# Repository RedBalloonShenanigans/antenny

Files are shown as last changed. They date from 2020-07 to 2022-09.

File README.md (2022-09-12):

# Antenny

Make your own base station to communicate with satellites!

We have a [discord server](https://discord.com/invite/nsSMEdv) for collaboration, questions, and show and tell off!

## Setting up the hardware

### Important Notice:
- Pin conflict: Do NOT use the folloing pins for GPIO if you are using SPIRAM firmware:
```
# known_confilit_pins = [
#     0, 1, 3, 6, 7, 
#     8, 9, 10, 11, 12, 
#     13, 16, 17, 20, 24, 
#     28, 29, 30, 31
# ]
```
- Pin that is input only
```
# input_only_pins = [34, 35, 36, 37, 38, 39]
```

### Jumpers

#### Required Antenny Jumpers
- On the antenny MK7 there are two required jumpers, labeled `JUMPER FOR PWN DR` on the back of the board. This will 
bridge the GPIO to the on board PWM Driver. 

#### Optional Antenny Jumpers

- The antenny MK7 provides jumpers to breakout pins 4, 26, 27, VCC and GND to the header labeled `P11` for the IMU. 
To use this header, you must solder the jumpers labeled `JUMPER FOR IMU`, otherwise, just used the ESP32 GPIO headers.

- To use wifi, either provide a antenna to the ESP32s on board jack, or solder the jumper next to the antenna 
connector labeled `R15` on the ESP32. See below picture. 

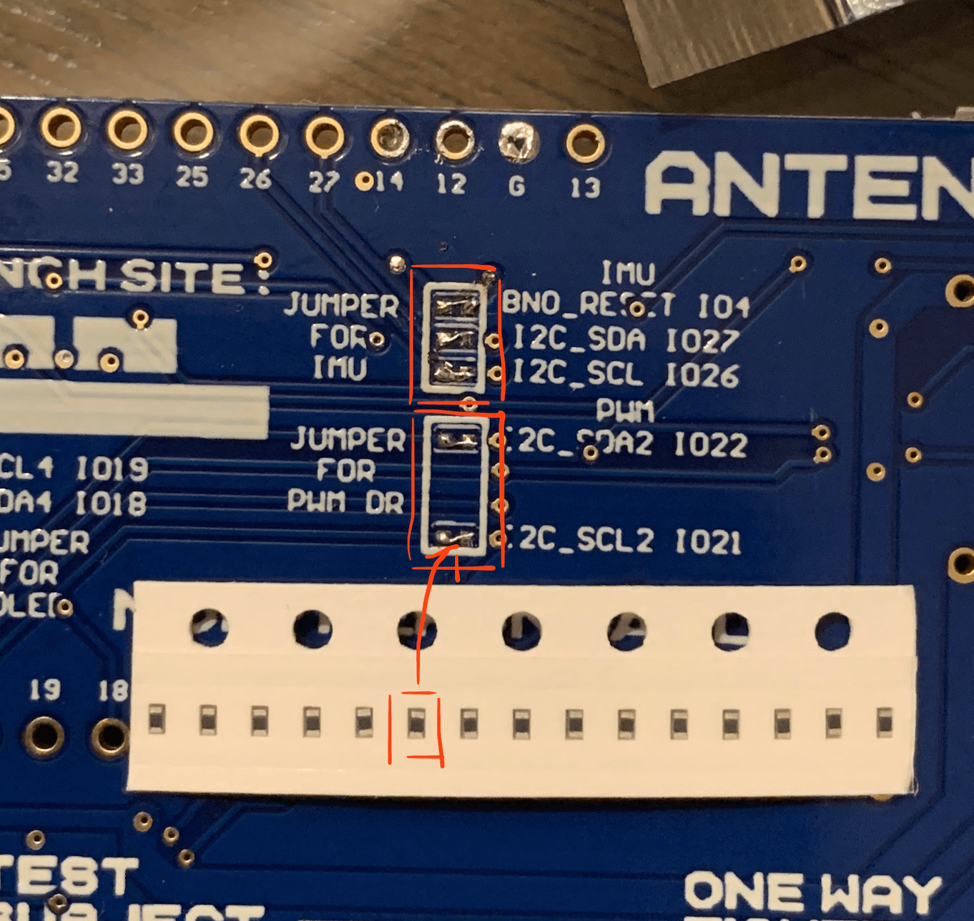
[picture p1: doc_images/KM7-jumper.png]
Antenny KM7 jumper

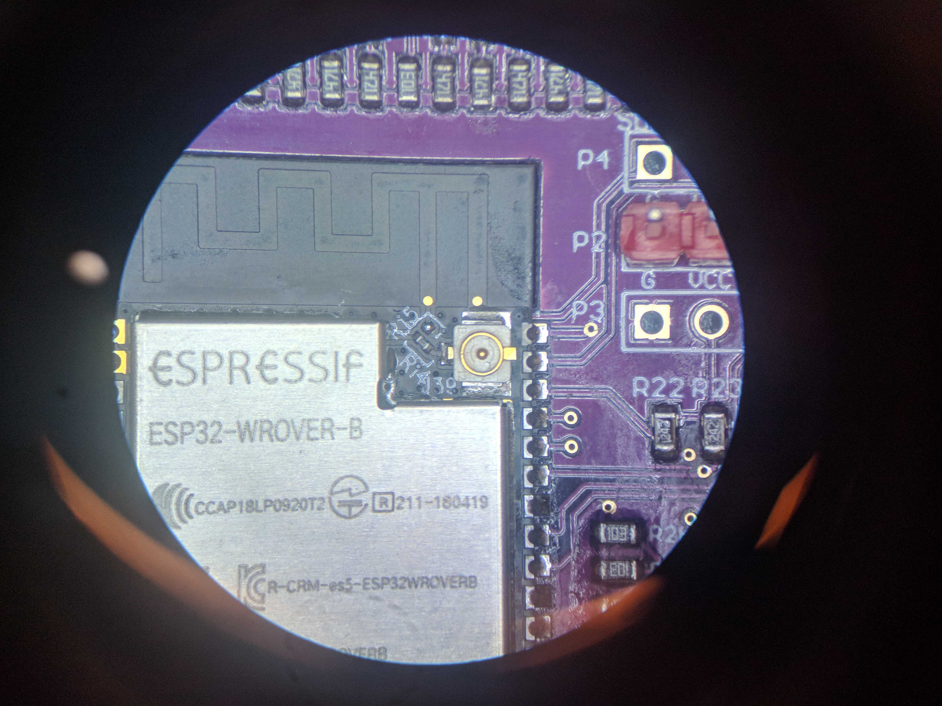
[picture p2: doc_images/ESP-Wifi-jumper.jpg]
Antenny KM7 jumper


- Important: When you start to program the Antenny board with esptool, please hold the K2 Tact Button until the program detect the download mode.

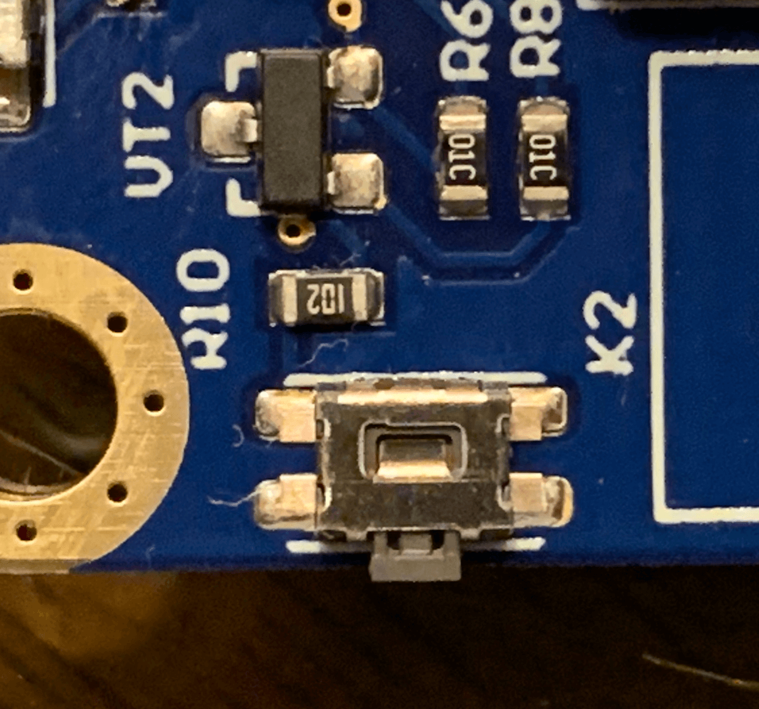
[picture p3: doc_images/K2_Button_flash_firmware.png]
Flash Firmware button


#### Optional IMU Jumper
There is one optional IMU jumper. This is used to select the IMU mode. More info can be found in the [BNO080 
datasheet](https://cdn.sparkfun.com/assets/1/3/4/5/9/BNO080_Datasheet_v1.3.pdf)
If you do not want to use the jumper, you can use pins to select the correct mode. This can also be useful for 
switching between modes in software. 

The mode we use is the Robotic Vacuum Cleaner (RVC) mode. To enable this you can provide power to the PS0 pin using 
the jumper as shown below. 

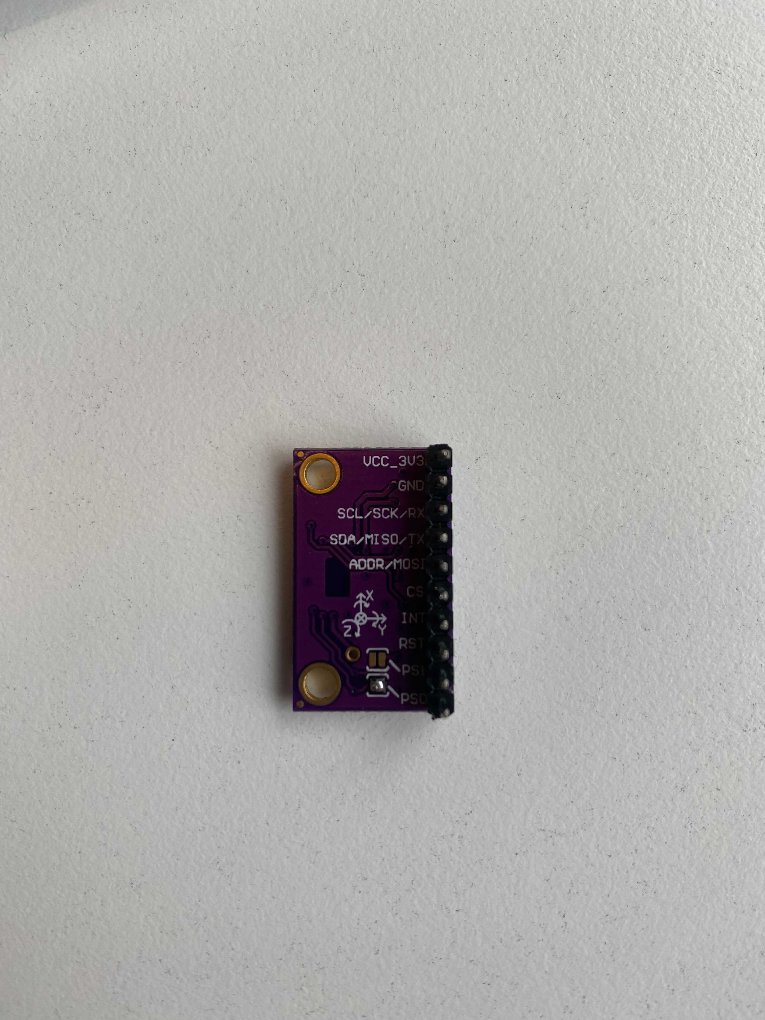
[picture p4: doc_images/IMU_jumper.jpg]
BNO080 Jumper


### Setting up the platform
This will go over how to setup the servo gimbal, IMU and antenny board. I used hot glue to secure the hardware, but 
more creative approaches are welcome. 

####Step 1: Position the IMU
Position the IMU on the gimbal arm. The position show below will give the correct orientation. If you want a 
different IMU position, you can correct the elevation angle in software. 

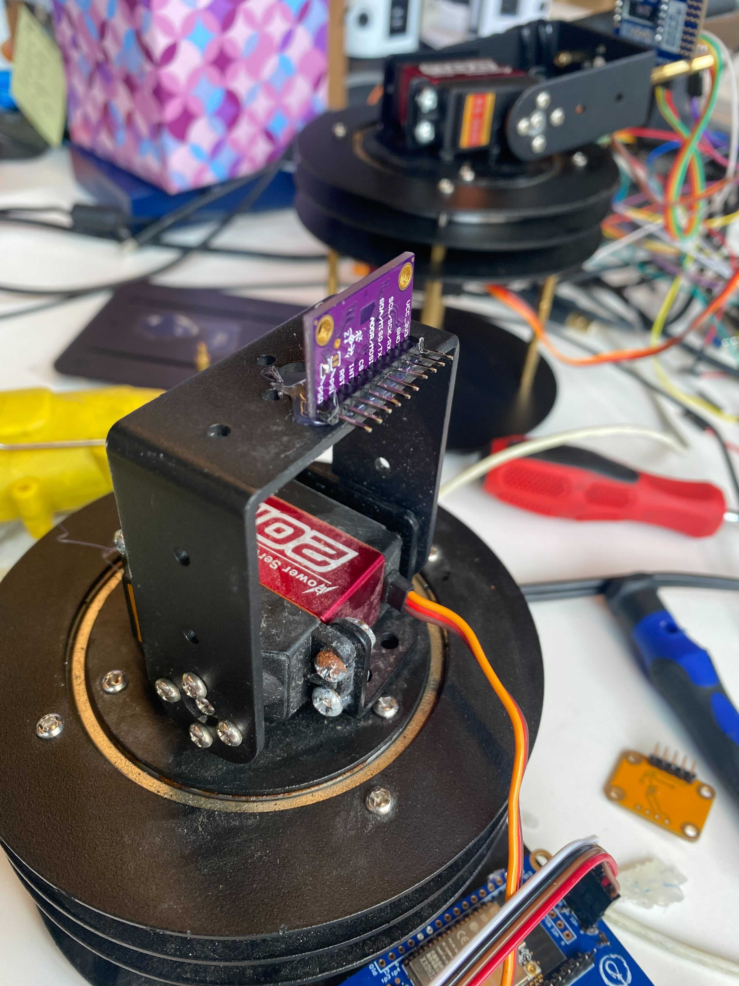
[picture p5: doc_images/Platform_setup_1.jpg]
Platform Step 1


#### Step 2: Position the Antenny
Next we secure the Antenny to the platform. It is advised to isolate the pins from any metal contact.

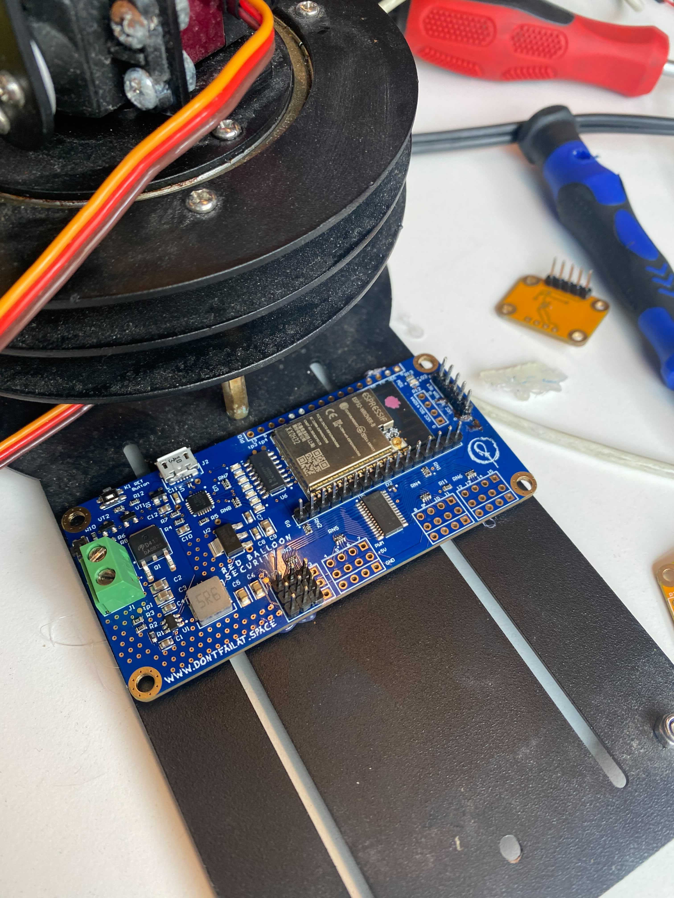
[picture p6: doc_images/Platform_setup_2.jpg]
Platform Step 2


### Step 3: Wire the IMU Communication Lines
NOTE: From this point on, the pins you use are configurable from the `antenny_config`, as described in the software 
guide below. To verify your pins or reconfigure as you wish, it is suggested you edit the config through the 
`antenny_manual_setup` command described in the software guide. 

The IMU communication lines are labeled on both the IMU PCB and the Antenny PCB, just match them up, as shown. 

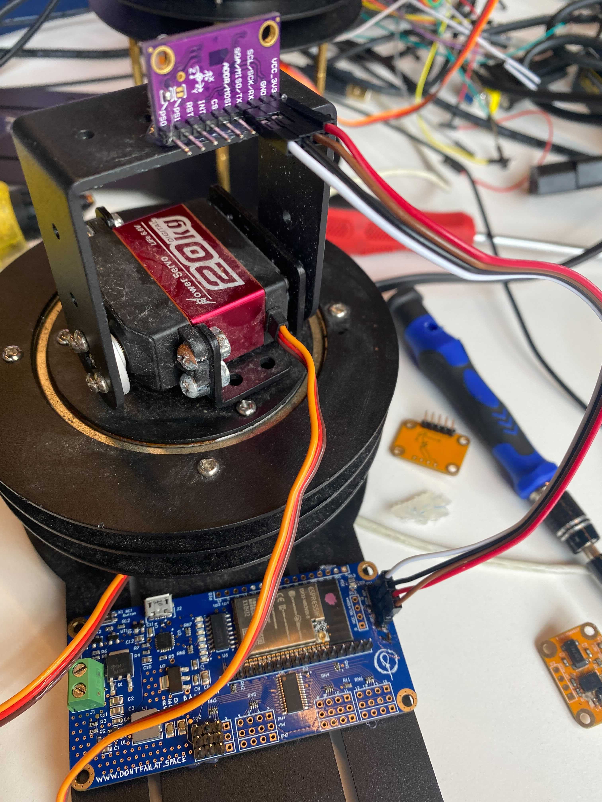
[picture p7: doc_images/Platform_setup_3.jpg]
Platform Step 3


### Step 4: Wire the IMU Reset Line
Same as step 3, it is labeled.

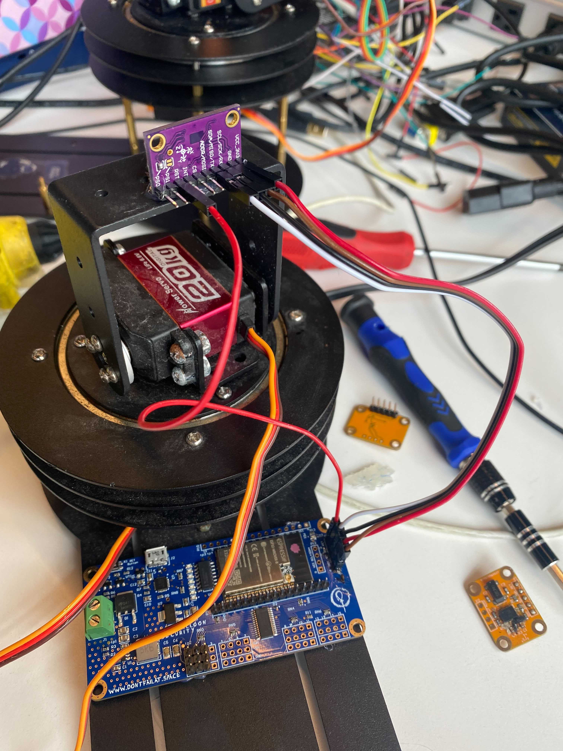
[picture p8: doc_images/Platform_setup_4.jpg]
Platform Step 4


### Step 5: Wiring the Program Select Pins (Optional):
If you did not solder the IMU jumper, you must pick two pins to use to control PS0 and PS1. If using this approach, 
its suggested you setup these pins using the `antenny_manual_setup`. 

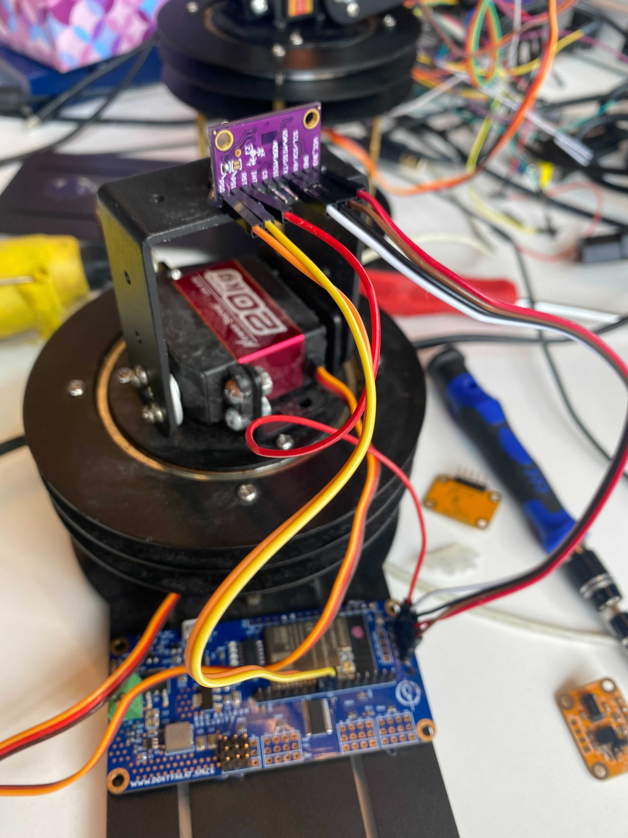
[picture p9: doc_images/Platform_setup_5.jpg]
Platform Step 5


### Step 6: Wiring the Servos
Next we wire the servos to the PWM controller. By default the elevation(top) servo goes to pwm index 0 and azimuth
(bottom) goes to index 1, but this is, again, configurable. 

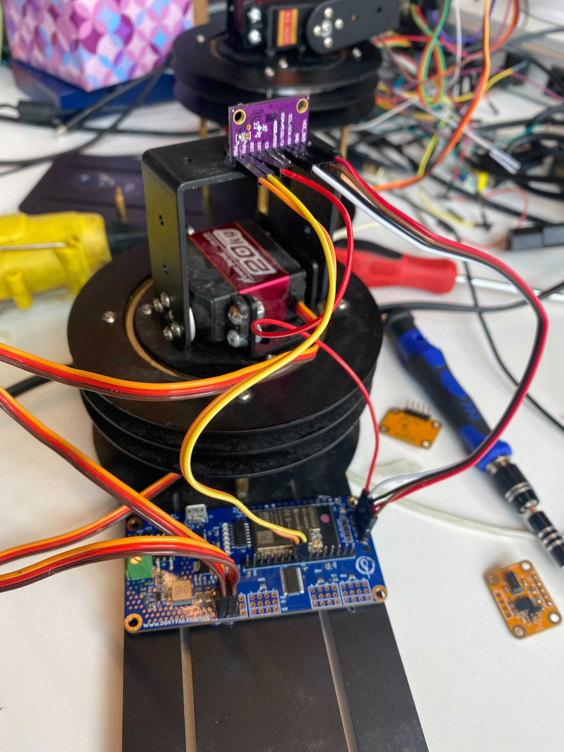
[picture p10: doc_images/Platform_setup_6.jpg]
Platform Step 6


# Installing the Antenny software

## Installing Micropython
1. Download and install the USB driver for the CP210 USB to UART chip [here](https://www.silabs.com/developers/usb-to-uart-bridge-vcp-drivers)

2. Download esptool from [here](https://github.com/espressif/esptool/)

3. Put the ESP into download mode (see above) and erase your ESP32

    Example: ```python3 -m esptool --port /dev/tty.SLAB_USBtoUART erase_flash```
    
4. Download the micropython firmware from [here](https://micropython.org/resources/firmware/esp32spiram-20210623-v1.16.bin)

5. Put the ESP into download mode (see above) and re-flash the Micropython firmware

    Example: ```python3 -m esptool --chip esp32 --port /dev/tty.SLAB_USBtoUART --baud 115200 
write_flash -z 0x1000 ~/Downloads/esp32spiram-20210623-v1.16.bin```

## Installing Antenny MP Code
0. We use MPFShell to upload the python files to the board. First you must install this on your host computer with 
`python3 -m pip install mpfshell`.
1. To begin install, first push the reset button on the antenny board, labeled `RET Button`.
2. Next, from the root directory of this repository, run  the `make nyansat` make directive with the `SERIAL` 
argument pointing to your antenny block device.

    Example: `make nyansat SERIAL=/dev/tty.SLAB_USBtoUART`
3. The Installer will give you a series of prompts.
    - `Do you want to do an installation of all components and libraries?(Y/n)`
    
        - If this is your first install, or you would like to do a fresh install of all code select `Y`, otherwise, 
        if you would only like to install specific components select `N`.
        
    - If you selected `Y` for the previous prompt you will see:
    
        - `Are you sure you want to erase all files on the device? (y/N)`
    
            - This is just a confirmation, as a full install will take a bit of time.
        
    - If you selected `N` you will see:
    
        - `Name a component you wish to install:`
        
            - If you are developing new components or making fixes to existing ones, you can upload one component at 
            a time by typing its name into this prompt. That name should correspond to a sub directory found in the 
            [station](https://github.com/RedBalloonShenanigans/antenny/tree/master/nyansat/station) directory. For 
            example selecting `imu` would upload all code in the [imu](https://github.com/RedBalloonShenanigans/antenny/tree/master/nyansat/station/imu) sub directory.
            
        - `Do you wish to install more? (y/N)`
        
            - Use this to repeat the above step.
            
        - `Do you want to keep the configs on the device? (Y/n)`. 
        
            - If you would like to restart your antenny configs from the repository state, select `N`, to keep your 
            configs on board select `Y`. 
            
        - `Do you want to re-install the libraries (y/N)`
        
            - Select yes to reinstall the libraries found [here](https://github.com/RedBalloonShenanigans/antenny/tree/master/lib)
            
4. You should see the installer upload the code to the antenny. 

5. You will see the installer report `False` upon completion, press `Enter` to continue.

6. The installer will prompt you for your WiFi info. If the above steps were taken to enable WiFi, enter your info, 
otherwise leave blank.

Your installation is complete!     

# Getting Started

## Entering the Python interpreter

1. Using a terminal utility of your choice, enter the devices python interpreter.

    - Examples:

        `screen <block device> 115200`
        
        or
        
        `minicom -D <block device> -b 115200`
        
    - In the case of windows, Putty is suggested.

2. Upon entering the interpreter you should be met with the python prompt `>>>`. If you are not try the reset button 
on the side of the board or revisit the `Installing Micropython` section of this README.

3. To view any potential import errors, press the reset button on the board as described in the installation section. 

     - In micropython, the first script run on startup will always be `boot.py` followed by `main.py`. 
     The `main.py` script will import all relevant antenny code and provide access to `api`, an instance of 
[AntennyAPI](https://github.com/RedBalloonShenanigans/antenny/blob/master/nyansat/station/api/api.py). 

## Using the Antenny API

### Device Startup

Once your hardware is properly setup and you have installed the antenny station code, you can begin working with the 
device. To interface with the device from the python interpreter, we will use member methods of the `api` class. 

#### High Level Methods

High level methods start with `antenny_` are used to setup your antenny assembly, calibrate and save calibration data. 

- `api.antenny_init_components()`

    - Initializes the components described by the current config. For more info on device configuration, please see 
    the "Configuring Antenny" section. 
    
- `api.antenny_calibrate()`

    - Calibrates the antenny platform. 
    - NOTE: This will start the automatic calibration routine. Currently, IMU calibration only supported by the BNO055 
    IMU. BNO080 support expected soon.
    
- `api.antenny_save(name: Optional)`

    - Saves the current configuration of each component as default. With an optional name. Makes the state of the 
    configuration and calibration persistent. 
    
- `api.antenny_manual_setup()`

    - This will walk you through manual configuration of the antenny board and its components. Useful if it is your 
    first time setting up, or for easier access to some of the more useful config entries.

#### Platform Methods

Platform methods start with `platform_` and are used to operate the platform, a term used in this project to describe 
the pwm driver, the motors it is driving, the IMU and the antenny board as a single assembly. 

- `api.platform_orient()`
 
    - Orients the platform to its current position. Should be run after repositioning the gimbal platform. This finds
     the 90 degree dead zone of the azimuth servo.
     
- `api.platform_start()`

    - Enables movement of the platform. Commands can be issued to point at specific coordinates.
    
- `api.platform_stop()`

    - Disables movement of the platform. Commands can be issues to manually move the servods or re-orient the platform.
    
- `api.platform_set_azimuth(az: int)`

    - Sets the azimuth coordinate of the platform while movement is enabled. 
    
- `api.platform_set_elevation(el: int)`

    - Sets the azimuth coordinate of the platform while movement is enabled. 

- `api.platform_set_coordinates(az: int, el: int)`

    - Sets both coordinates of the platform while movement is enabled.
    
#### Servo Methods

Each individual servo can be operated manually through these methods. Without access to the IMU the servos will not 
know they're orientation.

- `api.elevation_servo_set_position`
- `api.azimuth_servo_set_position`

    - Sets the position of the elevation servo. The current specs for the servos provided with the antenny put the 
    position argument in range(0, 4096), however only a subset of that range will actually move the servo.
    
- `api.elevation_servo_set_min_max(min: int, max: int)`
- `api.azimuth_servo_set_min_max(min: int, max: int)`

    - Sets the minimum and maximum `position` arguments that allow the servo to move, part of the higher level 
    calibration step. 

#### IMU Methods

IMU data can be accessed directly from the API as well. 

- `api.imu_get_azimuth()`

    - Returns the azimuth in degrees as reported by the IMU
    
- `api.imu_get_elevation()`

    - Returns the elevation in degrees as reported by the IMU
    
- `api.imu_get_euler()`

    - Returns the euler angles in order of yaw, roll, pitch. 
    
The IMU can also be manually calibrated

- `api.imu_calibrate()`

    - Begins the calibration routine. For best results, follow the printed instructions from the console. 
    
#### Other

There are plenty of other methods, most used for debugging, available to the user, as well as direct access to 
underlying components. For more information, reading through the antenny code is advised.      

### Configuring Antenny
NOTE: These configs have wrappers to properly alter the config members before saving in the API. In general only the 
High Level `api.antenny_save(name: Optional)` should be used by users. 

Your hardware is described by a series of 
[configs](https://github.com/RedBalloonShenanigans/antenny/tree/master/nyansat/station/configs) that can be updated 
through your installer or on the antenny board itself. This section will go over on baord config modification. To use 
the installer re-visit the above guide.

The api uses the 
[Config](https://github.com/RedBalloonShenanigans/antenny/blob/master/nyansat/station/config/config.py) class to 
manage configs and are exposed by the `AntennyAPI`. There are currently three configs used by the antenny system, but
 any components that require information to be stored across boots should use its own config.
 
#### Antenny API Config classes
    
- `api.antenny_config`
    - The [antenny_config](https://github.com/RedBalloonShenanigans/antenny/tree/master/nyansat/station/configs/antenny) 
describes the base station integration with pin connections as well as high-level attributes like current longitude and latitude.
    - Help information for each antenny_config member can be retrieved via `api.antenny_config_help()`

- `api.imu_config`
    - The [imu_config](https://github.com/RedBalloonShenanigans/antenny/tree/master/nyansat/station/configs/imu) 
    describes calibration data of the IMU. Currently only available for the BNO055, for more details on this you can 
    view the BNO055 and BNO08x data sheets.

- `api.servo_config`
    - The [servo_config](https://github.com/RedBalloonShenanigans/antenny/tree/master/nyansat/station/configs/servo) 
    describes the limits of the servo motors.

#### Config Methods

- `Config.set(<member>, <value>)`: Sets a config to a new value.

- `Config.get(<member>)`: Gets the current value of a config member.

- `Config.save(name: Optional)`: Saves the current config to the device, with a new name option for multiple configs.

- `Config.load(name: Optional)`: Loads the currently saved values, if name is specified, loads from a previously 
saved config, if it is not, reloads the last save of the current config.

- `Config.save_as_default_config()`: The current config will be loaded on reboot. 

- `Config.load_default_config()`: Load the config that was present on reboot.

## The Antenny Host System
Under Development...

Cooperation between the antenny board and another system is possible through the antenny client as well as the UDP 
Sender. Use of the client is not suggested while developing on or debugging the system, but could be useful for more 
interesting applications such as beacon tracking. 

### The Command Invoker
The `command_invoker` is a 1:1 library to the antenny `api` class found at `nyansat/host/shell/command_invoker.py`. The 
`command_invoker` calls out to the board through MPFShell to exec API commands. Feedback and error handling does not 
work very well so work should be offloaded to the board when possible. 

### Antenny Client
The `antenny_client`, found at `nyansat/host/shell/antenny_client.py` should use the command invoker to implement 
higher level functions in conjunction with more computationally expensive libraries. 

### Shell
Current depricated. 

The antenny client can then be integrated into the MPFShell environment through `nyansat/host/shell/__main__.py`. 
Commands of the format `do_<cmd>()` will be used as shell commands. See the file for examples. This shell can then be
 run through the command `make nyanshell`.

## Known Issues
- The BNO08x calibration never finishes :(
- The BNO08x euler angles are incorrect (maybe calibration, maybe I'm bad at math, probably both.)

##Requirements

- Python >= 3.6

NyanShell:

- MPFShell
- TUI-DOM

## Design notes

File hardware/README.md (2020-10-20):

# RBS Antenny Board 

If you want make your life a little simpler, we have a custom PCB for you! The Antenny board was designed and assembled by Red Balloon Security and you the ability to plug and play the NyanSat basic station with one single board and no complex wiring. Antenny combines the EPS32 (with Bluetooth and WIFI support), a 16 channel PWM driver, and a motor driver with a maximum output of maximum 27W at 6V. The RBS Antenny board can easily handle the movement control of NyanSat antenna gimbal, and you can load your own custom code to adjust it however you like. The onboard reserved I2C channel connectors allow you to extend the basic NyanSat setup with an RBS custom made IMU module, OLED screen and GPS module. After DEF CON, you can even repurpose the board for your future projects requiring microcontrollers and motor drivers.

The RBS Antenny board is designed using Altium Designer and Assembled by in-house pick and place machine in Manhattan, New York. Hardware design will be open sourced through our [GitHub repo](https://github.com/RedBalloonShenanigans/antenny/tree/master/hardware), and you can buy them in our store [link[. Feel free to check it out or make your own!  

## required items that are NOT included in package

- [Jumper Wires](https://www.amazon.com/EDGELEC-Breadboard-Optional-Assorted-Multicolored/dp/B07GD2BWPY/)
- [pin headers](https://www.amazon.com/MCIGICM-Header-2-45mm-Arduino-Connector/dp/B07PKKY8BX/)
- Soldering Iron Kit
- Power supply (6v-30v) or lipo battery

## Antenny board hardware setup guide and schematic

- [Setup guide and import updates](https://github.com/RedBalloonShenanigans/antenny/tree/master/hardware/Antenny_board_hardware_setup_guide.pdf)
Antenny V2 and V3 board have the similar pin layout. Please use this Antenny V2 Guide as reference.

- [Antenny V1 Board Schematic](https://github.com/RedBalloonShenanigans/antenny/tree/master/hardware/Antenny_V1_Schematic.pdf)

- [Antenny V2 Board Schematic](https://github.com/RedBalloonShenanigans/antenny/tree/master/hardware/Antenny_V2_Schematic.pdf)

- [Antenny V3 Board Schematic](https://github.com/RedBalloonShenanigans/antenny/tree/master/hardware/Antenny_V3_Schematic.pdf)

- [Antenny V5 Board Schematic](https://github.com/RedBalloonShenanigans/antenny/tree/master/hardware/Antenny_V5_Schematic.pdf)

- [IMU V2 Board Schematic](https://github.com/RedBalloonShenanigans/antenny/tree/master/hardware/IMU_V2_Schematic.pdf)

- [Antenny V3 Board Gerber files and NC Drill files for PCB manufacuture](https://github.com/RedBalloonShenanigans/antenny/tree/master/hardware/Gerber_NC_Drill_Antenna_base_v3)

- [Antenny V5 Board Gerber files and NC Drill files for PCB manufacuture](https://github.com/RedBalloonShenanigans/antenny/tree/master/hardware/Gerber_NC_Drill_Antenna_base_v5)

- [IMU v2 Board Gerber files and NC Drill files for PCB manufacuture](https://github.com/RedBalloonShenanigans/antenny/tree/master/hardware/Gerber_NC_Drill_IMU_standalone_v2)

## Antenny_board folder

These folder contains the RBS Antenny Board Altium Designer source file. 

- Antenna_base_v1

Verison 1.0 of RBS Antenny Board Layout

P6 GND; P5 VCCV6; P4 PWM

- Antenna_base_v2

Verison 2.0 of RBS Antenny Board Layout

- Antenna_base_v3

Verison 3.0 of RBS Antenny Board Layout

## IMU_board folder 

These folder contains the IMU board Altium Designer source file. 

- IMU_board_v1

Verison 1.0 of RBS IMU Board Layout

- IMU_board_v2

Verison 2.0 of RBS IMU Board Layout

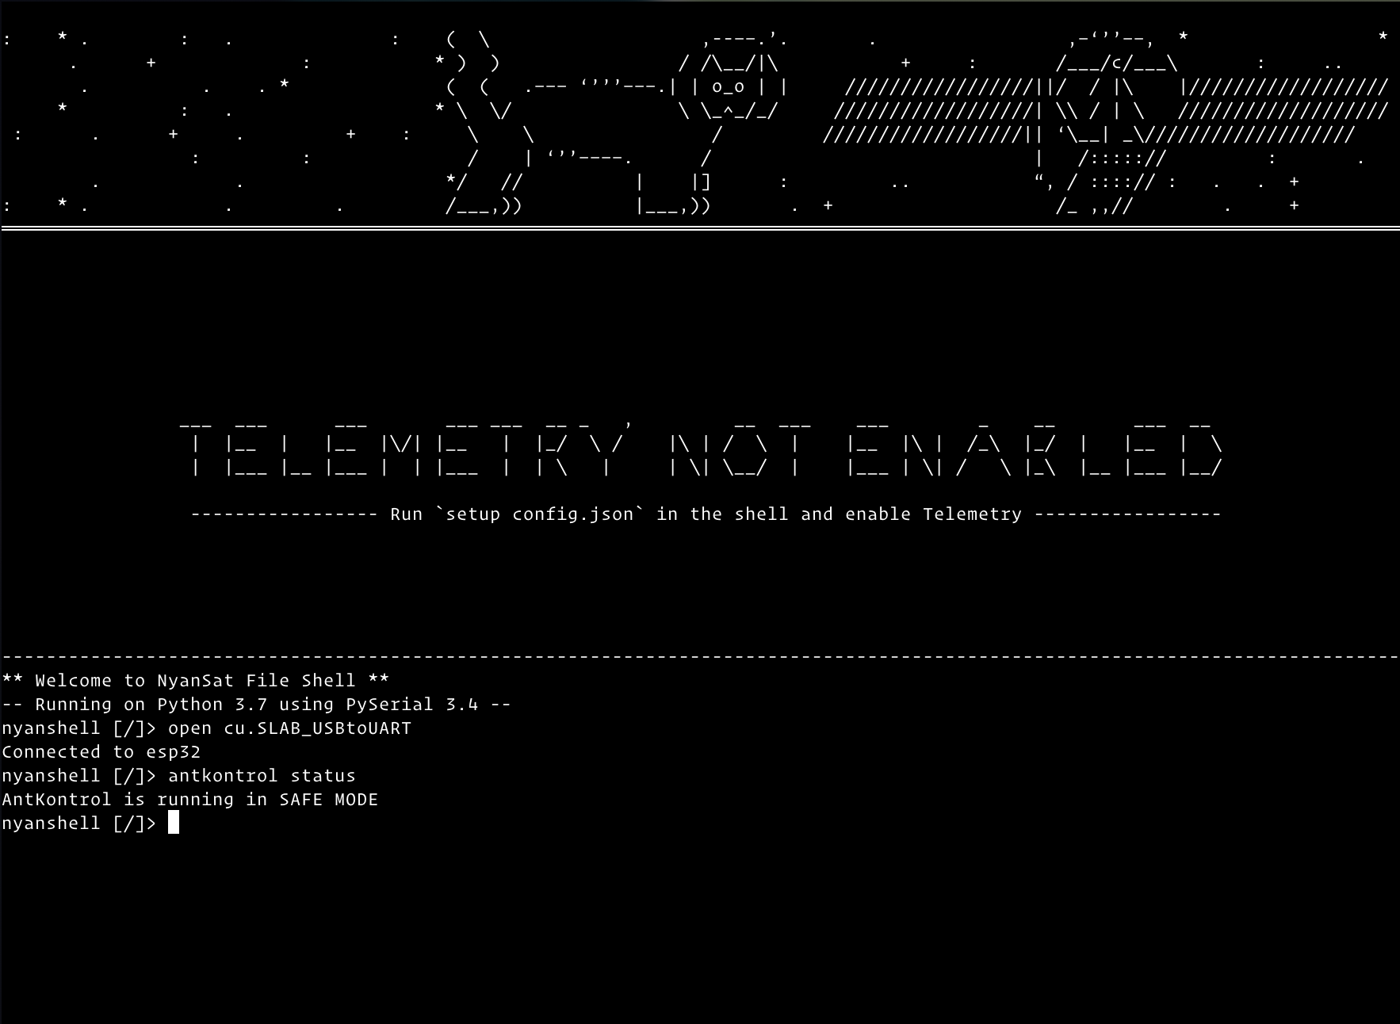
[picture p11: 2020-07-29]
doc_images/safe_mode.png

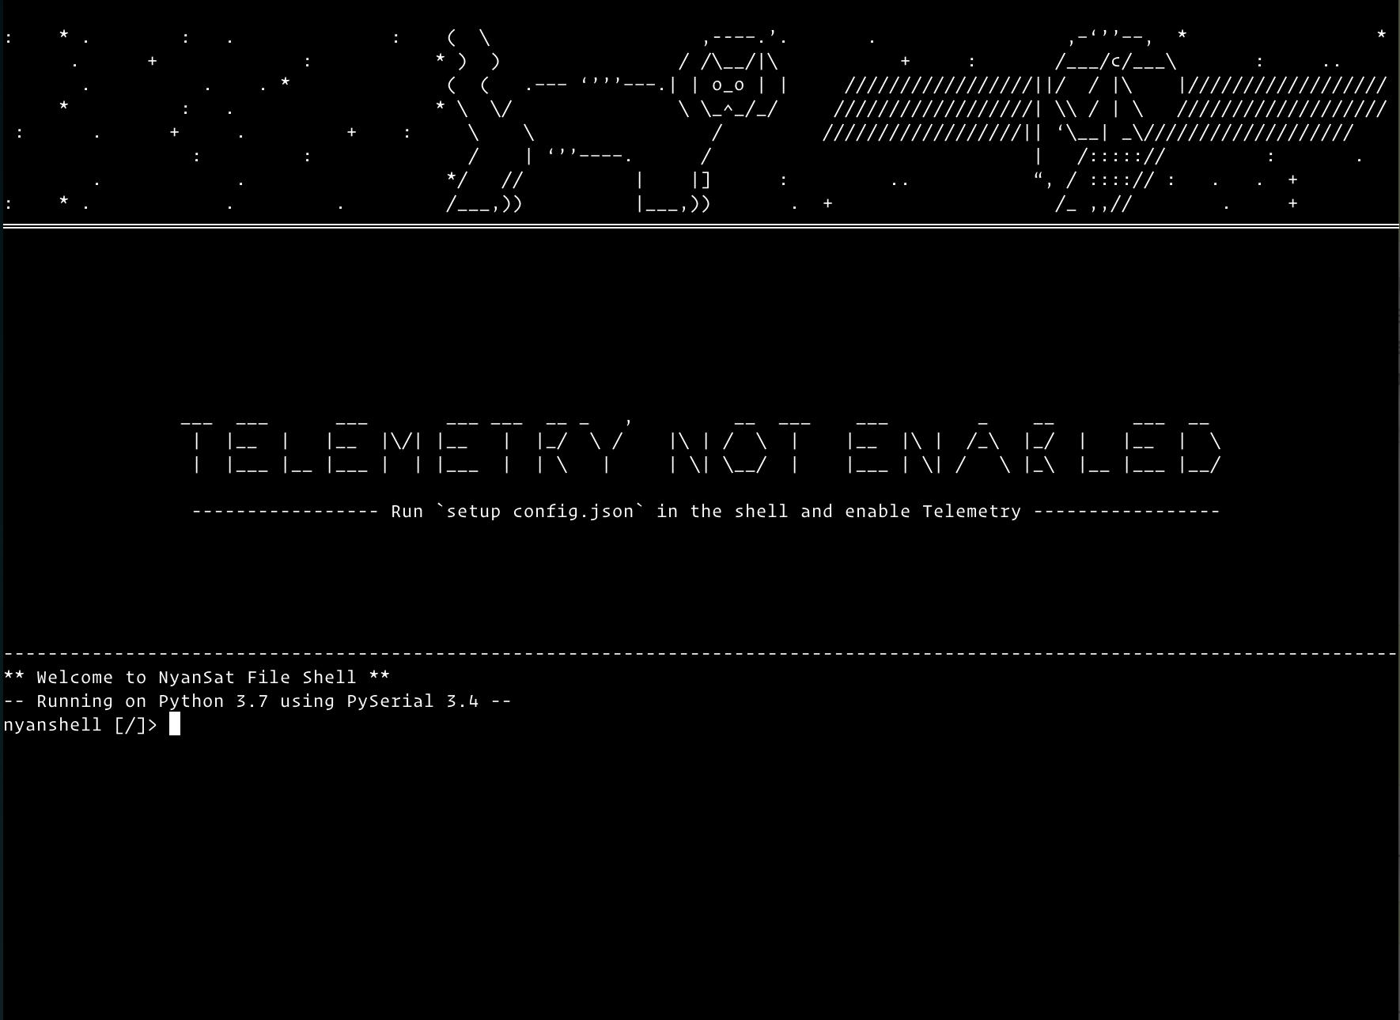
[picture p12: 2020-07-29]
doc_images/start_terminal.png

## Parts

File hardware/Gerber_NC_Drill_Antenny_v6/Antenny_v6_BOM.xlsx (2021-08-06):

Comment | Description | Designator | Footprint | LibRef | Quantity
LED0603_BLUE | LED BLUE CLEAR CHIP SMD | 1, 2, 3, 4, 5, 6, 7, D3 | FP-LTST-C191TBKT-MFG | CMP-22017-000008-1 | 8
C0603_0.1UF | 0603 0.1uF 50 Volts X7R 10% | C1, C4, C10, C12 | FP-C0603C-CF-IPC_B | C0603 | 4
C0805_10UF | 10 µF, 25 V, 0805 [2012 Metric], ± 20%, X5R | C2, C3, C9 | FP-C0805C-DN-IPC_A | C0805 | 3
C0805_22uF | 22 µF, 10 V, 0805 [2012 Metric], ± 20%, X7S | C5, C6 | FP-C0805C-DN-IPC_A | C0805 | 2
C0603_1UF | 0603 1 uF 50 V X5R ±10% | C7 | FP-C0603C-CF-IPC_B | C0603 | 1
C0603_4.7UF | CAP CER 4.7UF 0603 | C8, C11 | FP-C0603C-CF-IPC_B | C0603 | 2
SP0503BAHTG | TVS Diode Array, 30 pF, 30 KV, -40 to 85 degC, 4-Pin SOT143, RoHS, Tape and Reel | D1 | LFUS-SOT143-4_V | CMP-2000-05191-1 | 1
UCLAMP3311T | SEMTECH - UCLAMP3311T.TCT - TVS ARRAY, 40W, 3.3V, BI-DIRECTIONAL, SLP1006P2T | D2 | SEMT-SLP1006P2-2_V | TVS_CLAMP | 1
282836-2 | Female Header, Pitch 5 mm, 1 x 2 Position, Height 10 mm, Tail Length 3.5 mm, Rohs, Bulk | J1 | TECO-282836-2_V | CMP-1684-00017-1 | 0 | NC
473460001 | CONN RCPT USB2.0 MICRO B SMD R/A | J2 | FP-473460001-MFG | CMP-2000-05246-2 | 1
Jumper | Resistor | J3, J4, J5, J6, J7, J8, J9 | 0402-0R | Jumper | 0 | NC
SKSCLAE010 | Black Button Tactile Switch, Single Pole Single Throw (SPST) 50 mA 0.65mm Surface Mount | K1, K2 | ButtonTACT_3.5*3.55_90 | ButtonTACT | 2
0650_5.6UH | 0650_5.6UH, made in china | L1 | FP-SRP6540-MFG | SRP6540 | 1
ESP32-WROVER-IB (16MB) | SMD MODULE, ESP32-D0WDQ6 | MD1 | FP-ESP32-WROVER-MFG | CMP-194065-000005-1 | 1
Header 4 | Header, 4-Pin | P1, P3, P6, P7, P12 | HDR1X4 | Header 4 | 0 | NC
Header 4X2 | Header, 4-Pin, Dual row | P2, P4, P5, P8 | HDR2X4 | Header 4X2 | 0 | NC
Header 16 | Header, 16-Pin | P9, P10 | HDR1X16 | Header 16 | 0 | NC
Header 5 | Header, 5-Pin | P11 | HDR1X5 | Header 5 | 0 | NC
AOD417_PMOS-TO-252-DARP | AOD417 Trans MOSFET P-CH 30V 25A 3-Pin(2+Tab) DPAK | Q1 | DPAK228P994X240_3N | PMOS | 1
R0603_30R | 30Rohm 0603 | R1 | RESC1609X55X30LL15T15 | R0603 | 1
R0603_52.3K | 0603 52.3K Ohm | R2 | RESC1609X55X30LL15T15 | R0603 | 1
R0603_10K | 10K Ohm, 1%, 0.1W, 0603 | R3, R4, R5, R6, R7, R8, R11, R12 | RESC1609X55X30LL15T15 | R0603 | 8
R0603_1K | 0603 1K Ohm | R9, R10, R13 | RESC1609X55X30LL15T15 | R0603 | 3
YC124_10K | YC124-JR-0710KL (RES ARRAY 4 RES 10K OHM 0804) | RN1, RN2 | YC124 | YC124 | 2
YC124_1K | YC124-FR-071KL (RES ARRAY 4 RES 1K OHM 0804) | RN3, RN4, RN5, RN6, RN7, RN8 | YC124 | YC124 | 6
TPS56339DDCR | PWR MGMT SPECIALIZED REGULATOR | U1 | FP-DDC0006A-MFG | CMP-04918-000012-1 | 1
MCP1826S-3302E/DB | 1000 mA, Low Voltage, Low Quiescent Current LDO Regulator, 3-Pin SOT-223, Extended Temperature | U2 | SOT-223-DB3_L | CMP-0136-00504-1 | 1
CP2102N-A02-GQFN24 | USBXpress(TM) Family, 4 GPIOs, 2.2 to 3.6 V, -40 to 85 degC, 24-Pin QFN, RoHS | U3 | SLAB-QFN-24-2550x2550TP_A_V | CMP-2000-07570-1 | 1
comm_choke | EXC14CE900U | U4 | EXC14CE900U | comm_choke | 1
PCA9685PW,112 | 16-Channel, 12-Bit PWM Fm+ I2C-Bus LED Controller, 2.3 to 5.5 V, -40 to 85 degC, 28-Pin TSSOP (SOT361-1), RoHS, Tape and Reel | U5 | SOT361-1_V | CMP-1595-00004-2 | 1
ULN2003ADR | High-Voltage, High-Current Darlington Transistor Array, 0.5 A, 50 V, -20 to 70 degC, 16-Pin SOIC (D), Green (RoHS & no Sb/Br), Tape and Reel | U6 | D0016A_M | CMP-2000-04953-1 | 1
S8050 | Surface mount NPN transistor, package SOT-23 | VT1, VT2 | SMT_TRIODE_NPN | SMT_TRIODE_NPN | 2

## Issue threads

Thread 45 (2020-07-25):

V1 vs V2 vs Breadboard configs differ

cameronbosnic, 2020-07-25:
Not sure how you want to handle it  but the pin configs are different per board now with the most recent update.  You can't load a custom config with the nyansat console until antkontrol is initialized, which it can't do because the setup fails.

cameronbosnic, 2020-07-25:
I'd recommend changing the load order to allow a config to be loaded before initialization happens, and have 3 default pin configs that folks can load depending on which version of the hardware they have.

ruffruffruffie, 2020-07-28:
Thank you for bringing this issue up; to address this, we are:
- Creating a special "SAFE MODE" operating condition for AntKontrol
- Decoupling the configuration system from AntKontrol
- Providing more thorough documentation to help users set up their devices

In addition, we will be looking into your 3 default pin configuration solution!

cameronbosnic, 2020-08-01:
Ok, yeah like the safe mode idea.  Saw that you were doing a refactor. Thanks!

ruffruffruffie, 2020-08-03:
Hey cameronbosnic! We're staging in the 3 default pin configuration idea for today; we plan on including 2 additional configuration files for the `diy` and `av1` options to complement the default configuration, which reflects Antenny V2's pins.

cameronbosnic, 2020-08-06:
Linking back to the commit https://github.com/RedBalloonShenanigans/antenny/commit/cc01d3cf4b61a988bb08ef60eb8f5f911c65b000

ruffruffruffie, 2020-08-06:
Keen eye! We have started work around including an `antenny_board_version` parameter in the configurations to disable certain pins. To comprehensively address this issue, we are also going to add in the additional two configuration files; this should be a relatively simple addition.

ruffruffruffie, 2020-08-10:
Preloaded configuration files have been added!

Closed 2020-08-10.

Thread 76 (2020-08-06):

Create yagi config

cameronbosnic, 2020-08-06:
Yagis need to point 90' away from the current configuration.  Will help with some omnidirectional setups as well.

ruffruffruffie, 2020-08-06:
Interesting case! Do you have a diagram for the specific orientation of the antenna?

cameronbosnic, 2020-08-06:
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
vs
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

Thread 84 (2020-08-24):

ESP32 "slow serial" causes installation failures? (AttributeError: 'NoneType' object has no attribute 'ls' during make nyansat SERIAL=..))

conorpwr, 2020-08-24:
I know this isn't directly an antenny issue but given I had an issue with the ESP32 hardware suggested on the part list on the website, I thought I'd create an issue here for anyone else who ran into the same issue.

I was having repeated issues with trying to install the software on the ESP32 where it would throw an error for being unable to ls the ESP32 and throwing an exception:

```
make nyansat SERIAL=/dev/cu.usbserial-0001
git submodule update --init
cd lib/BNO055; git checkout 4422248bc82a79b4aec9cc90599f28de60e37c76
HEAD is now at 4422248 .cal_status returns bytearray to avoid allocation.
cd lib/PCA9685; git checkout 0fea2736f99a2840f0d644be866f6abd5bc14b48
HEAD is now at 0fea273 Updating readme for archiving
cd lib/micropython; git checkout c2317a3a8d5f184de2f816078d91be699274b94
M       tools/pyboard.py
HEAD is now at c2317a3a8 nrf/Makefile: Disable ROM text compression when compiling for debug.
cd lib/micropygps; git checkout 95b739381c8feb7c6b91b46db42646074c52a609
HEAD is now at 95b7393 Merge pull request #29 from donnyw/feature/gsv_util_function
cd lib/simple-pid; git checkout 7edd3d4c860cb02876ec455591f11193db18a94b
HEAD is now at 7edd3d4 Update changelog
python3 -m nyansat.station.installer /dev/cu.usbserial-0001
INFO:antenny_installer:Connecting to the device at /dev/cu.usbserial-0001
b'\x1b[0;32mI (539) cpu_start: Pro cpu up.\x1b[0m\r\n\x1b[0;32mI (539) cpu_start: Application information:\x1b[0m\r\n\x1b[0;32mI (539) cpu_start: Compile time:     Aug 20 2020 00:54:56\x1b[0m\r\n\x1b[0;32mI (542) cpu_start: ELF file SHA256:  0000000000000000...\x1b[0m\r\n\x1b[0;32mI (548) cpu_start: ESP-IDF:          v3.3.2\x1b[0m\r\n\x1b[0;32mI (553) cpu_start: Starting app cpu, entry point is 0x40082f30\x1b[0m\r\n\x1b[0;32mI (0) cpu_start: App cpu up.\x1b[0m\r\n\x1b[0;32mI (563) heap_init: Initializing. RAM available for dynamic allocation:\x1b[0m\r\n\x1b[0;32mI (570) heap_init: At 3FFAFF10 len 000000F0 (0 KiB): DRAM\x1b[0m\r\n\x1b[0;32mI (576) heap_init: At 3FFB6388 len 00001C78 (7 KiB): DRAM\x1b[0m\r\n\x1b[0;32mI (582) heap_init: At 3FFB9A20 len 00004108 (16 KiB): DRAM\x1b[0m\r\n\x1b[0;32mI (588) heap_init: At 3FFBDB5C len 00000004 (0 KiB): DRAM\x1b[0m\r\n\x1b[0;32mI (595) heap_init: At 3FFCA9E8 len 00015618 (85 KiB): DRAM\x1b[0m\r\n\x1b[0;32mI (601) heap_init: At 3FFE0440 len 00003AE0 (14 KiB): D/IRAM\x1b[0m\r\n\x1b[0;32mI (607) heap_init: At 3FFE4350 len 0001BCB0 (111 KiB): D/IRAM\x1b[0m\r\n\x1b[0;32mI (613) heap_init: At 4009DE28 len 000021D8 (8 KiB): IRAM\x1b[0m\r\n\x1b[0;32mI (620) cpu_start: Pro cpu start user code\x1b[0m\r\n\x1b[0;32mI (303) cpu_start: Starting scheduler on PRO CPU.\x1b[0m\r\n\x1b[0;32mI (0) cpu_start: Starting scheduler on APP CPU.\x1b[0m\r\nMicroPython v1.12-665-g60f5b941e on 2020-08-20; ESP32 module with ESP32\r\nType "help()" for more information.\r\n>>> '
WARNING:antenny_installer:Retrying to connect to the ESP32 device, attempt 0/3
b'ro cpu up.\x1b[0m\r\n\x1b[0;32mI (539) cpu_start: Application information:\x1b[0m\r\n\x1b[0;32mI (539) cpu_start: Compile time:     Aug 20 2020 00:54:56\x1b[0m\r\n\x1b[0;32mI (542) cpu_start: ELF file SHA256:  0000000000000000...\x1b[0m\r\n\x1b[0;32mI (548) cpu_start: ESP-IDF:          v3.3.2\x1b[0m\r\n\x1b[0;32mI (553) cpu_start: Starting app cpu, entry point is 0x40082f30\x1b[0m\r\n\x1b[0;32mI (0) cpu_start: App cpu up.\x1b[0m\r\n\x1b[0;32mI (563) heap_init: Initializing. RAM available for dynamic allocation:\x1b[0m\r\n\x1b[0;32mI (570) heap_init: At 3FFAFF10 len 000000F0 (0 KiB): DRAM\x1b[0m\r\n\x1b[0;32mI (576) heap_init: At 3FFB6388 len 00001C78 (7 KiB): DRAM\x1b[0m\r\n\x1b[0;32mI (582) heap_init: At 3FFB9A20 len 00004108 (16 KiB): DRAM\x1b[0m\r\n\x1b[0;32mI (588) heap_init: At 3FFBDB5C len 00000004 (0 KiB): DRAM\x1b[0m\r\n\x1b[0;32mI (595) heap_init: At 3FFCA9E8 len 00015618 (85 KiB): DRAM\x1b[0m\r\n\x1b[0;32mI (601) heap_init: At 3FFE0440 len 00003AE0 (14 KiB): D/IRAM\x1b[0m\r\n\x1b[0;32mI (607) heap_init: At 3FFE4350 len 0001BCB0 (111 KiB): D/IRAM\x1b[0m\r\n\x1b[0;32mI (613) heap_init: At 4009DE28 len 000021D8 (8 KiB): IRAM\x1b[0m\r\n\x1b[0;32mI (620) cpu_start: Pro cpu start user code\x1b[0m\r\n\x1b[0;32mI (303) cpu_start: Starting scheduler on PRO CPU.\x1b[0m\r\n\x1b[0;32mI (0) cpu_start: Starting scheduler on APP CPU.\x1b[0m\r\nMicroPython v1.12-665-g60f5b941e on 2020-08-20; ESP32 module with ESP32\r\nType "help()" for more information.\r\n>>> '
WARNING:antenny_installer:Retrying to connect to the ESP32 device, attempt 1/3
b'\x1b[0;32mI (539) cpu_start: Pro cpu up.\x1b[0m\r\n\x1b[0;32mI (539) cpu_start: Application information:\x1b[0m\r\n\x1b[0;32mI (539) cpu_start: Compile time:     Aug 20 2020 00:54:56\x1b[0m\r\n\x1b[0;32mI (542) cpu_start: ELF file SHA256:  0000000000000000...\x1b[0m\r\n\x1b[0;32mI (548) cpu_start: ESP-IDF:          v3.3.2\x1b[0m\r\n\x1b[0;32mI (553) cpu_start: Starting app cpu, entry point is 0x40082f30\x1b[0m\r\n\x1b[0;32mI (0) cpu_start: App cpu up.\x1b[0m\r\n\x1b[0;32mI (563) heap_init: Initializing. RAM available for dynamic allocation:\x1b[0m\r\n\x1b[0;32mI (570) heap_init: At 3FFAFF10 len 000000F0 (0 KiB): DRAM\x1b[0m\r\n\x1b[0;32mI (576) heap_init: At 3FFB6388 len 00001C78 (7 KiB): DRAM\x1b[0m\r\n\x1b[0;32mI (582) heap_init: At 3FFB9A20 len 00004108 (16 KiB): DRAM\x1b[0m\r\n\x1b[0;32mI (588) heap_init: At 3FFBDB5C len 00000004 (0 KiB): DRAM\x1b[0m\r\n\x1b[0;32mI (594) heap_init: At 3FFCA9E8 len 00015618 (85 KiB): DRAM\x1b[0m\r\n\x1b[0;32mI (601) heap_init: At 3FFE0440 len 00003AE0 (14 KiB): D/IRAM\x1b[0m\r\n\x1b[0;32mI (607) heap_init: At 3FFE4350 len 0001BCB0 (111 KiB): D/IRAM\x1b[0m\r\n\x1b[0;32mI (613) heap_init: At 4009DE28 len 000021D8 (8 KiB): IRAM\x1b[0m\r\n\x1b[0;32mI (620) cpu_start: Pro cpu start user code\x1b[0m\r\n\x1b[0;32mI (303) cpu_start: Starting scheduler on PRO CPU.\x1b[0m\r\n\x1b[0;32mI (0) cpu_start: Starting scheduler on APP CPU.\x1b[0m\r\nMicroPython v1.12-665-g60f5b941e on 2020-08-20; ESP32 module with ESP32\r\nType "help()" for more information.\r\n>>> '
WARNING:antenny_installer:Retrying to connect to the ESP32 device, attempt 2/3
INFO:antenny_installer:Connected, welcome to the Antenny installer!
Are you sure you want to erase all files on the device at /dev/cu.usbserial-0001? (y/N) y
Traceback (most recent call last):
  File "/usr/local/Cellar/python/3.7.7/Frameworks/Python.framework/Versions/3.7/lib/python3.7/runpy.py", line 193, in _run_module_as_main
    "__main__", mod_spec)
  File "/usr/local/Cellar/python/3.7.7/Frameworks/Python.framework/Versions/3.7/lib/python3.7/runpy.py", line 85, in _run_code
    exec(code, run_globals)
  File "/Users/conor/code/esptool2/antenny/nyansat/station/installer/__main__.py", line 324, in <module>
    installer.install(only_core_reinstall=args.core_install)
  File "/Users/conor/code/esptool2/antenny/nyansat/station/installer/__main__.py", line 276, in install
    self._clean_files(ignore_lib=only_core_reinstall)
  File "/Users/conor/code/esptool2/antenny/nyansat/station/installer/__main__.py", line 78, in _clean_files
    files = self._file_explorer.ls()
AttributeError: 'NoneType' object has no attribute 'ls'
make: *** [nyansat] Error 1
```

Based on what was discussed in https://github.com/scientifichackers/ampy/issues/19 I edited the enter_raw_repl function with pyboard.py for mpfshell to add in a time.sleep(2) immediately after the first self.con.write(b"\r\x03\x03") and then another time.sleep(2) after the first while section as per that GitHub issue. So it now looks something like this:

```
    def enter_raw_repl(self):

        time.sleep(0.5)   # allow some time for board to reset
        self.con.write(b"\r\x03\x03")  # ctrl-C twice: interrupt any running program
        time.sleep(2)

        # flush input (without relying on serial.flushInput())
        n = self.con.inWaiting()
        while n > 0:
            self.con.read(n)
            n = self.con.inWaiting()
        time.sleep(2)
```

Once that change was made the install appeared to work perfectly. Based on some dubious adds of print() statements to various sections, my theory is that for whatever reason this ESP32 seems to respond slower then expected and the output didn't match what was expected (the code was looking for a > when it was still showing intro messages) and threw an error. The baud rate was left at 115200 as well. Hope this helps anyone who might be running into a similar issue.

ruffruffruffie, 2020-10-07:
Hi conorpwr! Thanks for noting this issue and providing a potential solution; we really appreciate it! Just to confirm, is this problem localized to `mpfshell`? If so, I suggest we open an issue in their repository and address this issue at the root. Additionally, we can add safeguards in our installation script for the timebeing!

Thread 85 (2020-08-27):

Please export gerbers to allow for easy duplication

pk-r7, 2020-08-27:
Could you please export gerbers to allow for easy fabrication using oshpark or a similar service? I exported v2 using a temp license but do not have a full license to export the newest versions. The version I created as a prototype is missing the mask areas for the USB connector, which has been corrected in a newer version.

0xac, 2020-08-28:
Yup, we'll do that tomorrow. Hans is also rolling out v3, which now uses a
ESP32 module with additional SPI RAM.

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

pk-r7, 2020-10-15:
Gerbers exported

Closed 2020-10-15.

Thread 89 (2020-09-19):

Cannot connect to host celestrak.com:443

benb0jangles, 2020-09-19:
on MacOS 10.12.6

I'm getting:

ClientConnectorCertificateError: Cannot connect to host celestrak.com:443 ssl:True [SSLCertVerificationError: (1, '[SSL: CERTIFICATE_VERIFY_FAILED] certificate verify failed: unable to get local issuer certificate (_ssl.c:1108)')]

Any reason?

benb0jangles, 2020-09-25:
```
Traceback (most recent call last):
  File "/Library/Frameworks/Python.framework/Versions/3.8/lib/python3.8/site-packages/aiohttp-4.0.0a1-py3.8-macosx-10.9-x86_64.egg/aiohttp/connector.py", line 916, in _wrap_create_connection
    return await self._loop.create_connection(*args, **kwargs)  # type: ignore  # noqa
  File "/Library/Frameworks/Python.framework/Versions/3.8/lib/python3.8/asyncio/base_events.py", line 1050, in create_connection
    transport, protocol = await self._create_connection_transport(
  File "/Library/Frameworks/Python.framework/Versions/3.8/lib/python3.8/asyncio/base_events.py", line 1080, in _create_connection_transport
    await waiter
  File "/Library/Frameworks/Python.framework/Versions/3.8/lib/python3.8/asyncio/sslproto.py", line 529, in data_received
    ssldata, appdata = self._sslpipe.feed_ssldata(data)
  File "/Library/Frameworks/Python.framework/Versions/3.8/lib/python3.8/asyncio/sslproto.py", line 189, in feed_ssldata
    self._sslobj.do_handshake()
  File "/Library/Frameworks/Python.framework/Versions/3.8/lib/python3.8/ssl.py", line 944, in do_handshake
    self._sslobj.do_handshake()
ssl.SSLCertVerificationError: [SSL: CERTIFICATE_VERIFY_FAILED] certificate verify failed: unable to get local issuer certificate (_ssl.c:1108)

The above exception was the direct cause of the following exception:

Traceback (most recent call last):
  File "/Library/Frameworks/Python.framework/Versions/3.8/lib/python3.8/runpy.py", line 193, in _run_module_as_main
    return _run_code(code, main_globals, None,
  File "/Library/Frameworks/Python.framework/Versions/3.8/lib/python3.8/runpy.py", line 86, in _run_code
    exec(code, run_globals)
  File "/Users/benji/antenny/nyansat/host/shell/__main__.py", line 463, in <module>
    sys.exit(main())
  File "/Users/benji/antenny/nyansat/host/shell/__main__.py", line 457, in main
    nyanshell.cmdloop()
  File "/Library/Frameworks/Python.framework/Versions/3.8/lib/python3.8/cmd.py", line 138, in cmdloop
    stop = self.onecmd(line)
  File "/Library/Frameworks/Python.framework/Versions/3.8/lib/python3.8/cmd.py", line 217, in onecmd
    return func(arg)
  File "/Users/benji/antenny/nyansat/host/shell/errors.py", line 28, in wrapper
    func(*args, **kwargs)
  File "/Users/benji/antenny/nyansat/host/shell/__main__.py", line 326, in do_track
    self.client.track(sat_name)
  File "/Users/benji/antenny/nyansat/host/shell/errors.py", line 13, in wrapper
    func(*args, **kwargs)
  File "/Users/benji/antenny/nyansat/host/shell/antenny_client.py", line 135, in track
    asyncio.run(self._start_track(sat_name, (latitude, longitude)))
  File "/Library/Frameworks/Python.framework/Versions/3.8/lib/python3.8/asyncio/runners.py", line 43, in run
    return loop.run_until_complete(main)
  File "/Library/Frameworks/Python.framework/Versions/3.8/lib/python3.8/asyncio/base_events.py", line 616, in run_until_complete
    return future.result()
  File "/Users/benji/antenny/nyansat/host/shell/antenny_client.py", line 337, in _start_track
    tle_data_encoded = await SatelliteScraper.load_tle()
  File "/Users/benji/antenny/nyansat/host/satdata_client.py", line 28, in load_tle
    return await scraper.get_tle_lines()
  File "/Users/benji/antenny/nyansat/host/satdata_client.py", line 19, in get_tle_lines
    await self.get_tle_file()
  File "/Users/benji/antenny/nyansat/host/satdata_client.py", line 15, in get_tle_file
    async with session.get(source) as response:
  File "/Library/Frameworks/Python.framework/Versions/3.8/lib/python3.8/site-packages/aiohttp-4.0.0a1-py3.8-macosx-10.9-x86_64.egg/aiohttp/client.py", line 963, in __aenter__
    self._resp = await self._coro
  File "/Library/Frameworks/Python.framework/Versions/3.8/lib/python3.8/site-packages/aiohttp-4.0.0a1-py3.8-macosx-10.9-x86_64.egg/aiohttp/client.py", line 442, in _request
    conn = await self._connector.connect(
  File "/Library/Frameworks/Python.framework/Versions/3.8/lib/python3.8/site-packages/aiohttp-4.0.0a1-py3.8-macosx-10.9-x86_64.egg/aiohttp/connector.py", line 507, in connect
    proto = await self._create_connection(req, traces, timeout)
  File "/Library/Frameworks/Python.framework/Versions/3.8/lib/python3.8/site-packages/aiohttp-4.0.0a1-py3.8-macosx-10.9-x86_64.egg/aiohttp/connector.py", line 838, in _create_connection
    _, proto = await self._create_direct_connection(
  File "/Library/Frameworks/Python.framework/Versions/3.8/lib/python3.8/site-packages/aiohttp-4.0.0a1-py3.8-macosx-10.9-x86_64.egg/aiohttp/connector.py", line 983, in _create_direct_connection
    raise last_exc
  File "/Library/Frameworks/Python.framework/Versions/3.8/lib/python3.8/site-packages/aiohttp-4.0.0a1-py3.8-macosx-10.9-x86_64.egg/aiohttp/connector.py", line 960, in _create_direct_connection
    transp, proto = await self._wrap_create_connection(
  File "/Library/Frameworks/Python.framework/Versions/3.8/lib/python3.8/site-packages/aiohttp-4.0.0a1-py3.8-macosx-10.9-x86_64.egg/aiohttp/connector.py", line 918, in _wrap_create_connection
    raise ClientConnectorCertificateError(
aiohttp.client_exceptions.ClientConnectorCertificateError: Cannot connect to host celestrak.com:443 ssl:True [SSLCertVerificationError: (1, '[SSL: CERTIFICATE_VERIFY_FAILED] certificate verify failed: unable to get local issuer certificate (_ssl.c:1108)')]

```

yuanzhewu, 2020-10-07:
This could be a issue of how OS X handle certificate for python3.8.

benb0jangles, 2020-11-21:
Install Certificates.command

https://stackoverflow.com/questions/42098126/mac-osx-python-ssl-sslerror-ssl-certificate-verify-failed-certificate-verify

Closed 2020-11-22.

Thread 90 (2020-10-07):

Wireless AP SSIDS/Passwords containing spaces fail in station/installer

rksh, 2020-10-07:
When attempting to re-configure my homebrew setup to a home wireless AP with an SSID and Password containing multiple space (0x20) characters.

It may worth checking other corner cases such as %2F, %3F, %21, and even possible unicode.

rksh, 2020-10-07:
proposed fix - works in testing, but probably not the most elegant way to do this. Provided as a proof-of-concept since I can't easily write a meaningful test case for this, and testing corner cases requires standing up and reconfiguring an 802.11 AP.

ruffruffruffie, 2020-10-07:
Hi there! I'm trying to replicate this issue and I am unable to do so; I've tried with SSIDs & password combinations with roughly 5 spaces. Do you have any additional pointers that I can test this bug with?

rksh, 2020-10-07:
oh no, this is going to end up being hardware/implementation specific, isn't it? Will dust off some old wireless hardware and do detailed testing.

setup that's known-bad:
Asus AC1200G WPA2 PSK, latest mfgr. firmware, 2 spaces in the SSID, 4 spaces in the password.
Micropython: esp32-idf3-20200902-v1.13.bin

rksh, 2020-10-22:
also worth noting that i'm using zsh under OSX.

rksh, 2020-10-29:
OK, finally stood up an old Apple Airport for testing!
SSID: "Antenny Wi-Fi Network"

With the password "Testing^5" - All good.
With the password "test test test" - no dice.

Worth noting that this is an old-as-dirt AP, but Apple has apparently updated it to support WPA2-PSK-CCMP (as registered in Android using WiGLE WiFi Wardriving) - haven't found a way to downshift it to WPA1 or WEP, they're aggressive about forcing pretty good defaults in their Airport Utility suite.

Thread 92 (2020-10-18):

Issue in upload calibration data

kernelpanic-bf, 2020-10-18:
When trying to use the command `upload_calibration` it seems to error out on my system. (See error below)

I think I found the mistake in the following line:
https://github.com/RedBalloonShenanigans/antenny/blob/9e33c643516e24bf92bb2269c7add5c64490afd9/nyansat/station/imu/imu_bno055.py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
`for register_name, register_address in self.CALIBRATION_REGISTERS:`
It needs to be changed to:
`for register_name, register_address in self.CALIBRATION_REGISTERS.items():`

```Traceback (most recent call last):
  File "/usr/lib/python3.8/runpy.py", line 194, in _run_module_as_main
    return _run_code(code, main_globals, None,
  File "/usr/lib/python3.8/runpy.py", line 87, in _run_code
    exec(code, run_globals)
  File "/home/kernelpanic/Projects/satelliteFun-20200817/4-Files/micropython/antenny2/antenny/nyansat/host/shell/__main__.py", line 463, in <module>
    sys.exit(main())
  File "/home/kernelpanic/Projects/satelliteFun-20200817/4-Files/micropython/antenny2/antenny/nyansat/host/shell/__main__.py", line 457, in main
    nyanshell.cmdloop()
  File "/usr/lib/python3.8/cmd.py", line 138, in cmdloop
    stop = self.onecmd(line)
  File "/usr/lib/python3.8/cmd.py", line 217, in onecmd
    return func(arg)
  File "/home/kernelpanic/Projects/satelliteFun-20200817/4-Files/micropython/antenny2/antenny/nyansat/host/shell/__main__.py", line 223, in do_upload_calibration
    self.client.upload_calibration()
  File "/home/kernelpanic/Projects/satelliteFun-20200817/4-Files/micropython/antenny2/antenny/nyansat/host/shell/errors.py", line 13, in wrapper
    func(*args, **kwargs)
  File "/home/kernelpanic/Projects/satelliteFun-20200817/4-Files/micropython/antenny2/antenny/nyansat/host/shell/antenny_client.py", line 153, in upload_calibration
    status = self.invoker.imu_upload_calibration_profile()
  File "/home/kernelpanic/Projects/satelliteFun-20200817/4-Files/micropython/antenny2/antenny/nyansat/host/shell/command_invoker.py", line 142, in imu_upload_calibration_profile
    return self.eval_string_expr("api.imu.upload_calibration_profile('calibration.json')")
  File "/home/kernelpanic/Projects/satelliteFun-20200817/4-Files/micropython/antenny2/antenny/nyansat/host/shell/nyan_pyboard.py", line 14, in eval_string_expr
    ret = self.exec_("print(eval({}))".format(command))
  File "/usr/local/lib/python3.8/dist-packages/mpfshell-0.9.1-py3.8.egg/mp/pyboard.py", line 156, in exec_
    raise PyboardError("exception", ret, ret_err)
mp.pyboard.PyboardError: ('exception', b'', b'Traceback (most recent call last):\r\n  File "<stdin>", line 1, in <module>\r\n  File "<string>", line 1, in <module>\r\n  File "imu/imu_bno055.py", line 171, in upload_calibration_profile\r\n  File "imu/imu_bno055.py", line 175, in _set_calibration_profile\r\nValueError: too many values to unpack (expected 2)\r\n')
```

benb0jangles, 2020-11-22:
upload calibration? Just run calibrate in shell and at the end it will save?

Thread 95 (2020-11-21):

track starlink-1743

benb0jangles, 2020-11-21:
command:
track starlink-1743

result:
Traceback (most recent call last):
  File "/usr/lib/python3.6/runpy.py", line 193, in _run_module_as_main
    "__main__", mod_spec)
  File "/usr/lib/python3.6/runpy.py", line 85, in _run_code
    exec(code, run_globals)
  File "/home/benji/antenny/nyansat/host/shell/__main__.py", line 463, in <module>
    sys.exit(main())
  File "/home/benji/antenny/nyansat/host/shell/__main__.py", line 457, in main
    nyanshell.cmdloop()
  File "/usr/lib/python3.6/cmd.py", line 138, in cmdloop
    stop = self.onecmd(line)
  File "/usr/lib/python3.6/cmd.py", line 217, in onecmd
    return func(arg)
  File "/home/benji/antenny/nyansat/host/shell/errors.py", line 28, in wrapper
    func(*args, **kwargs)
  File "/home/benji/antenny/nyansat/host/shell/__main__.py", line 326, in do_track
    self.client.track(sat_name)
  File "/home/benji/antenny/nyansat/host/shell/errors.py", line 13, in wrapper
    func(*args, **kwargs)
  File "/home/benji/antenny/nyansat/host/shell/antenny_client.py", line 135, in track
    asyncio.run(self._start_track(sat_name, (latitude, longitude)))
AttributeError: module 'asyncio' has no attribute 'run'

any ideas?

Setup:
Jetson Nano arm64
Ubuntu 18.4.5
Python 3.6.9

benb0jangles, 2020-11-22:
AttributeError: module 'asyncio' has no attribute 'run'

asyncio.run is new in Python 3.7 or above. jetson is using python 3.6.9
https://github.com/omnilib/aiomultiprocess/issues/21#issuecomment-492439725

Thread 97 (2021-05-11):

Using WEBrepl

benb0jangles, 2021-05-11:
Hi

Downloaded WebRepl from:
[https://github.com/micropython/webrepl](https://github.com/micropython/webrepl)

Connected to wifi:
`ESP32AccessPoint`

Opened:
`webrepl.html`

connected to:
ws://192.168.4.1:8266/

entered password

But what now?
-Is it possible to command the Tracker?
-Possible to calibrate?
-list configs?

How possible?

When I run commands:
`>>> help    `

I get:                                                                                                                  
`<function>     `

Then command:                                                                                                               
`>>> configs        `

I get:                                                                                                           
```
Traceback (most recent call last):                                                                                            
  File "<stdin>", line 1, in <module>                                                                                         
NameError: name 'configs' isn't defined
```

Also command:                                                                                      
`>>> setup 0                `

Gives:                                                                                                   
```
Traceback (most recent call last):                                                                                            
  File "<stdin>", line 1                                                                                                      
SyntaxError: invalid syntax                                                                                                   
>>>  
```

Why no worky plz?

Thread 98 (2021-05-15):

ImportError: cannot import name 'WebSocketConnectionClosedException' from 'websocket'

benb0jangles, 2021-05-15:
Help? Or Silence?

Running command:
`python3 -m nyansat.host.shell
`
Give error:
```
Traceback (most recent call last):
  File "/usr/lib/python3.9/runpy.py", line 197, in _run_module_as_main
    return _run_code(code, main_globals, None,
  File "/usr/lib/python3.9/runpy.py", line 87, in _run_code
    exec(code, run_globals)
  File "/home/benji2/antenny/nyansat/host/shell/__main__.py", line 6, in <module>
    from websocket import WebSocketConnectionClosedException
ImportError: cannot import name 'WebSocketConnectionClosedException' from 'websocket' (/usr/local/lib/python3.9/dist-packages/websocket/__init__.py)

```

amanbansal2709, 2021-08-10:
Hey, I think you may have resolved this issue by now and I am kinda stuck at the same thing to install nyansat on ESP32. Can you direct me if you have resolved this already?

DanPesce, 2021-08-10:
Hello, we have made many updates to the `station` code to make it more usable/reliable/understandable. That being said, the `host` code is now under construction. On a related note, I highly suggest using the python interpreter as described in the updated README to operate the device as it is still under development and the host shell hides/does not have acces to a lot of information and errors.

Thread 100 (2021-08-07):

Antennny MK7 Documentation

aeonik, 2021-08-07:
Hello,
I am trying to setup the Antenny MK7 from the Space access kit, but the getting started guide seems to be incomplete. I am not sure which headers need to be soldered, or where the connections need to be made. The gimbal that came with the kit also seems to be sized for a different board.

Regards,
Aeonik

SometimesCake, 2021-08-07:
Yeah the gimbal will need some mount point created to interface with the board. The jumpers you are looking for are on the main page, just scroll down and see the first picture. https://github.com/RedBalloonShenanigans/antenny

Basically all 5 jumpers on the back in the outline need to be connected.

aeonik, 2021-08-10:
I got the jumpers on fine. It's the next steps that I am unsure of.

For example, what to do with the IMU, or which headers need to be soldered on in order to drive the gimble.

I am also curious if there are recommended antennas.

DanPesce, 2021-08-10:
Hello, next steps should be to assemble your "platform". This entails plugging the servo gimbal into the PWM controller pins and the IMU to the I2C pins. The pins used for this are configurable and are described in [the antenny config](https://github.com/RedBalloonShenanigans/antenny/blob/master/nyansat/station/configs/antenny/default.json), or can be set during runtime using the command `api.antenny_config.set(<config member>, <pythonic_value>)`. Hope this helps!

cjearls95, 2021-08-10:
Is there any amount of breakout headers that should be populated for the motors? I planned on populating at minimum 2 sets of the groups of 4 along with the two ESP breakout header lengths and the two i2c breakouts.

DanPesce, 2021-08-10:
You are correct about which/how many. I currently have mine setup with PWM indexes 0 and 1 soldered.  These are the 3 pin connectors on the side of the board labeled PWM, +5V and GND. On your servo gimbal, the brown wire is GND. You can populate as many as you want, but bare minimum would be 2 x 6 pins for the servos and 5 pins total for VCC, GND, SCL (ESP pin 26), SDA (ESP pin 27) and RST(ESP pin 4) for the IMU, those pinouts are printed on the back of the board.

cjearls-soter, 2021-08-11:
Looking over the newly updated documentation, it looks like the picture of the ESP R14 is soldered for the WiFi, but the document says R15.

DanPesce, 2021-08-11:
There are two resistors, R14 and R15. R14 will connect to the antenna connector seen next to it, for the stock configuration a compatible antenna is required. R15 connects to the PCB antenna, but the resistor must be swapped to use it

cjearls95, 2021-08-12:
Awesome thank you. Additionally, what size screws did you guys use to secure the IMU and the antenna base? Don't want to damage my gimble. Would it be possible to add this into the GitHub documentation?

DanPesce, 2021-08-16:
I'll be putting up an assembly guide today, however the way you fix the board/imu to the gimbal is mostly up to you. I just used some M3 standoffs, washers and a bit of hot glue.

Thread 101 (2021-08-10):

nyansat package

amanbansal2709, 2021-08-10:
I am trying to install Antenny software onto your ESP32 and using 'make nyansat SERIAL=<your serial port>' from my windows cmd but it's not working. I read about it and it says nyansat is only for Linux based systems. is it true? If yes, Can you please advise me on how to move forward?
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

SometimesCake, 2021-08-10:
Look up how to setup WSL on your windows box, I haven't tried it but it could be a way for you to move forward.

DanPesce, 2021-08-10:
Hi, I have no tried on windows yet, but one issue is that you must run the `make` command from the repository root.

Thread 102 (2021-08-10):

Fresh install results in OSError: [Errno 2] ENOENT

aeonik, 2021-08-10:
Hello,
I followed the following steps:
```
esptool.py --port /dev/ttyUSB0 erase_flash
esptool.py --chip esp32 --port /dev/ttyUSB0 write_flash -z 0x1000 esp32spiram-20210623-v1.16.bin
make nyansat SERIAL=/dev/ttyUSB0
screen /dev/ttyUSB0 115200
```
After trying to boot I am getting the following error:
```
time.monotonic() not available in python < 3.3, using time.time() as fallback
Traceback (most recent call last):
  File "main.py", line 18, in <module>
  File "main.py", line 13, in start
  File "api/api.py", line 37, in __init__
  File "config/config.py", line 15, in __init__
  File "config/config.py", line 38, in _get_default_config
OSError: [Errno 2] ENOENT
MicroPython v1.14 on 2021-02-02; ESP32 module (spiram) with ESP32
Type "help()" for more information.
>>>
```

I have tried two different firmware versions:
- esp32spiram-20210623-v1.16.bin
- esp32spiram-idf3-20210202-v1.14.bin

Should I try a different firmware version, or is there some other way to work around this issue?

DanPesce, 2021-08-10:
Hi, I will make this more clear in the install steps as well as in the documentation, but on your first install, you should select `No` for `Do you want to keep the configs on the device? (Y/n)` as your device currently has no configs on it.

Closed 2023-05-20.

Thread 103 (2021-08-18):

"ModuleNotFoundError: No module named 'mp'" When running make command

InkRF, 2021-08-18:
When running the `make nyansat SERIAL=/dev/ttyUSB0` from the root directory of the repo , I retrieve the following error:
```python
Traceback (most recent call last):
  File "/usr/lib/python3.9/runpy.py", line 197, in _run_module_as_main
    return _run_code(code, main_globals, None,
  File "/usr/lib/python3.9/runpy.py", line 87, in _run_code
    exec(code, run_globals)
  File "/home/kali/antenny/nyansat/station/installer/__main__.py", line 13, in <module>
    from mp.mpfexp import RemoteIOError, ConError
ModuleNotFoundError: No module named 'mp'
```

While I haven't worked with Python before, I see that its missing or can't find several module/files in the repo. After commenting out line 13 in `./antenny/nyansat/station/installer/__main__.py` just to see what happens, it does the same again where it can't find the nyansat module.

I'm not quite sure what I should do from here, I've re-cloned the repo to no avail so now I'm coming here for guidance.
Cheers

DanPesce, 2021-08-18:
Hello, MPFShell is a dependency. It is used to interact with the antenny board from you host computer.  To install it you have to run `python3 -m pip install mpfshell`. If you haven't worked with python before you might also have to install pip. Instructions for this can be found [here](https://pip.pypa.io/en/stable/installation/).

InkRF, 2021-08-18:
Just got it sorted out, didn't have the mpfshell module installed on this computer. May be good to include that requirements in the README as well

DanPesce, 2021-08-18:
Yep, its mentioned at the tail end, but I will add it to the setup steps.

Closed 2021-08-18.

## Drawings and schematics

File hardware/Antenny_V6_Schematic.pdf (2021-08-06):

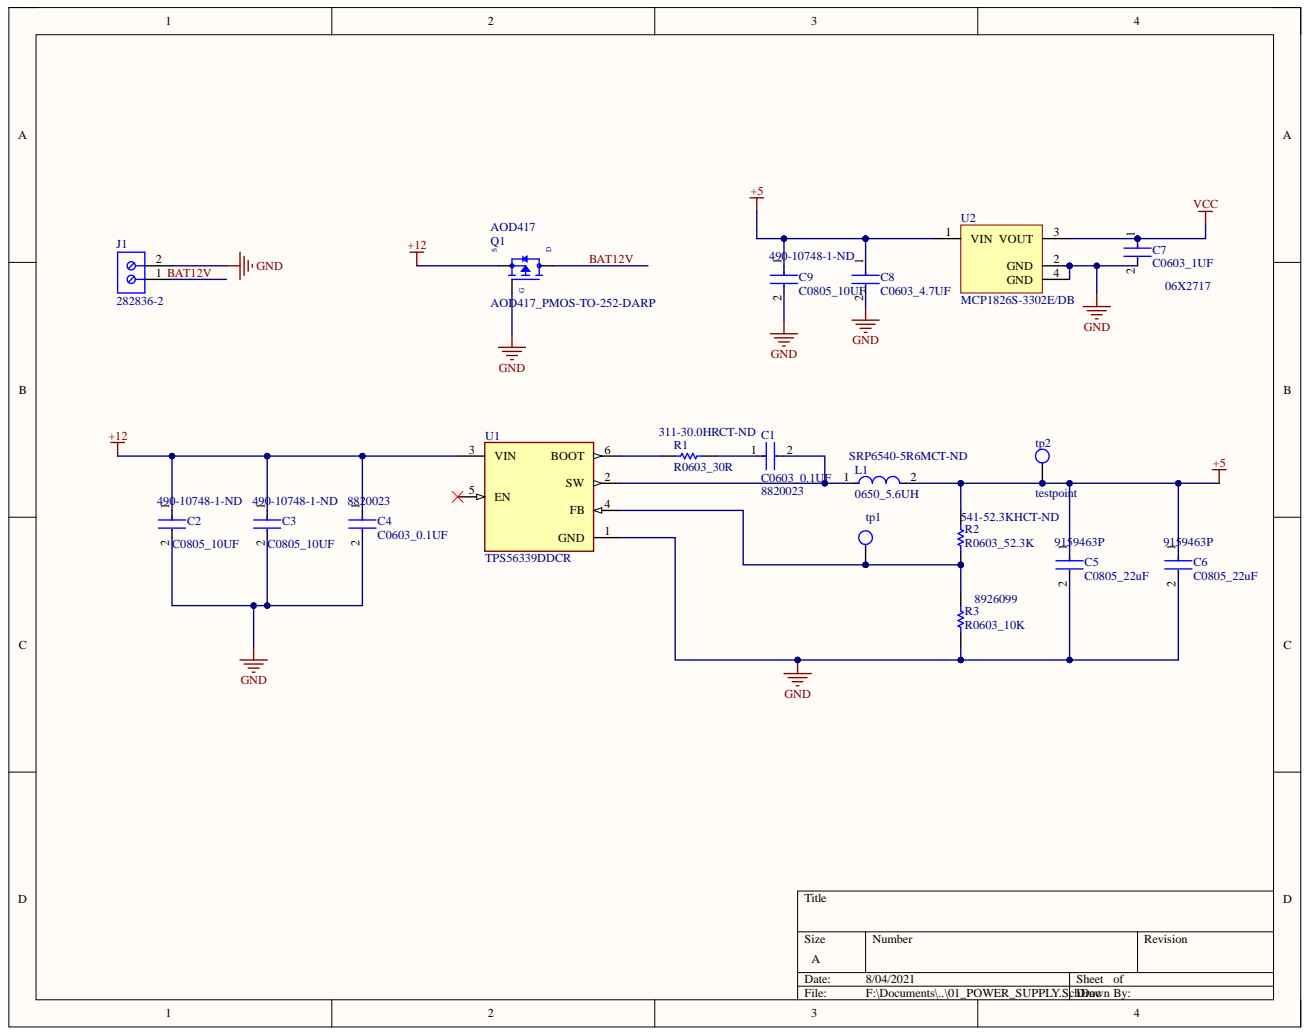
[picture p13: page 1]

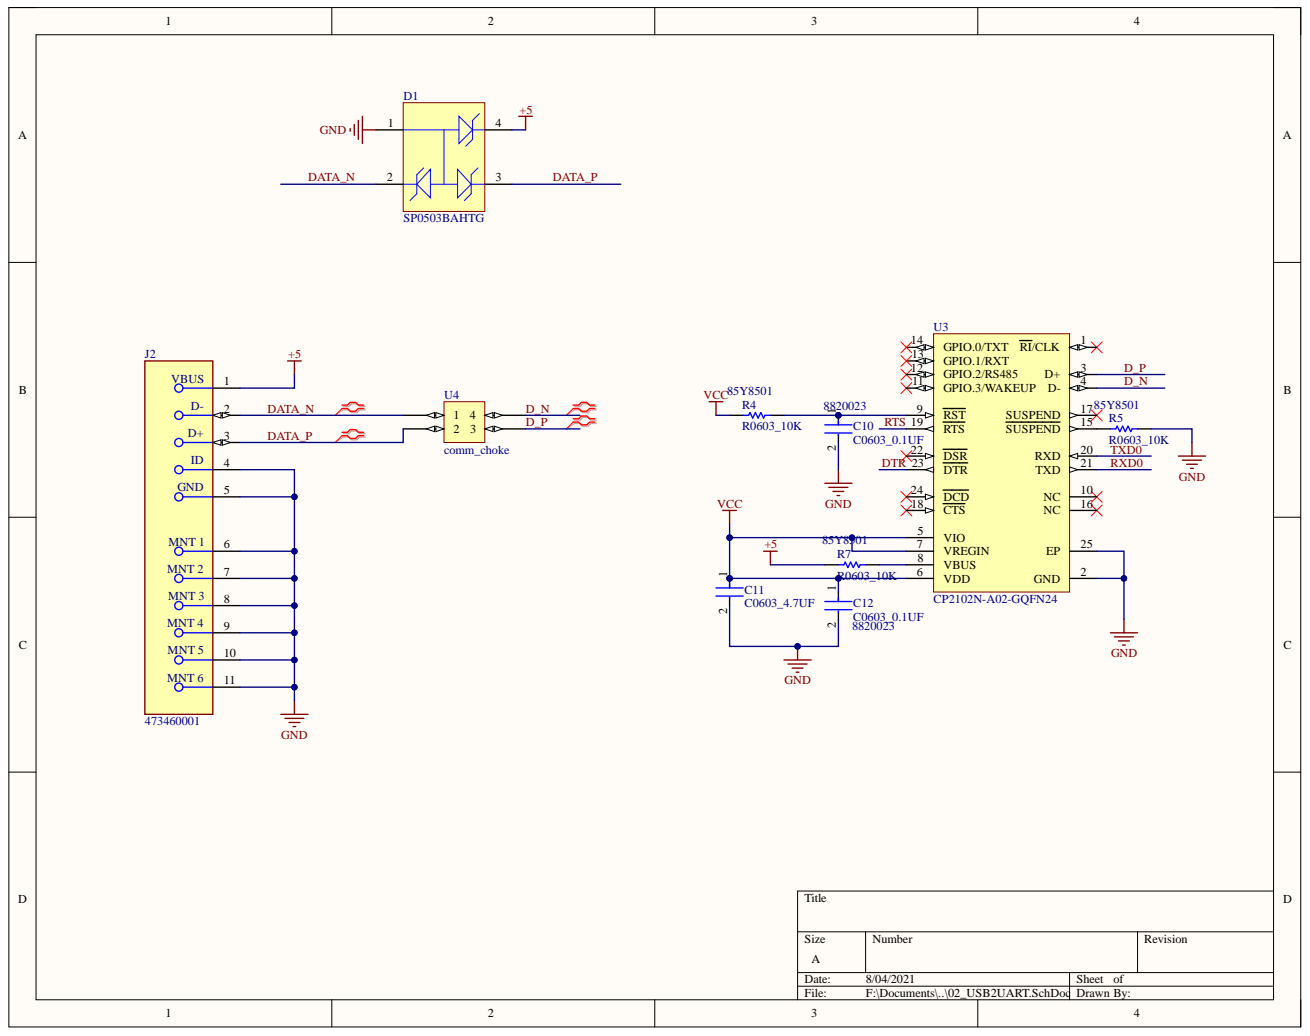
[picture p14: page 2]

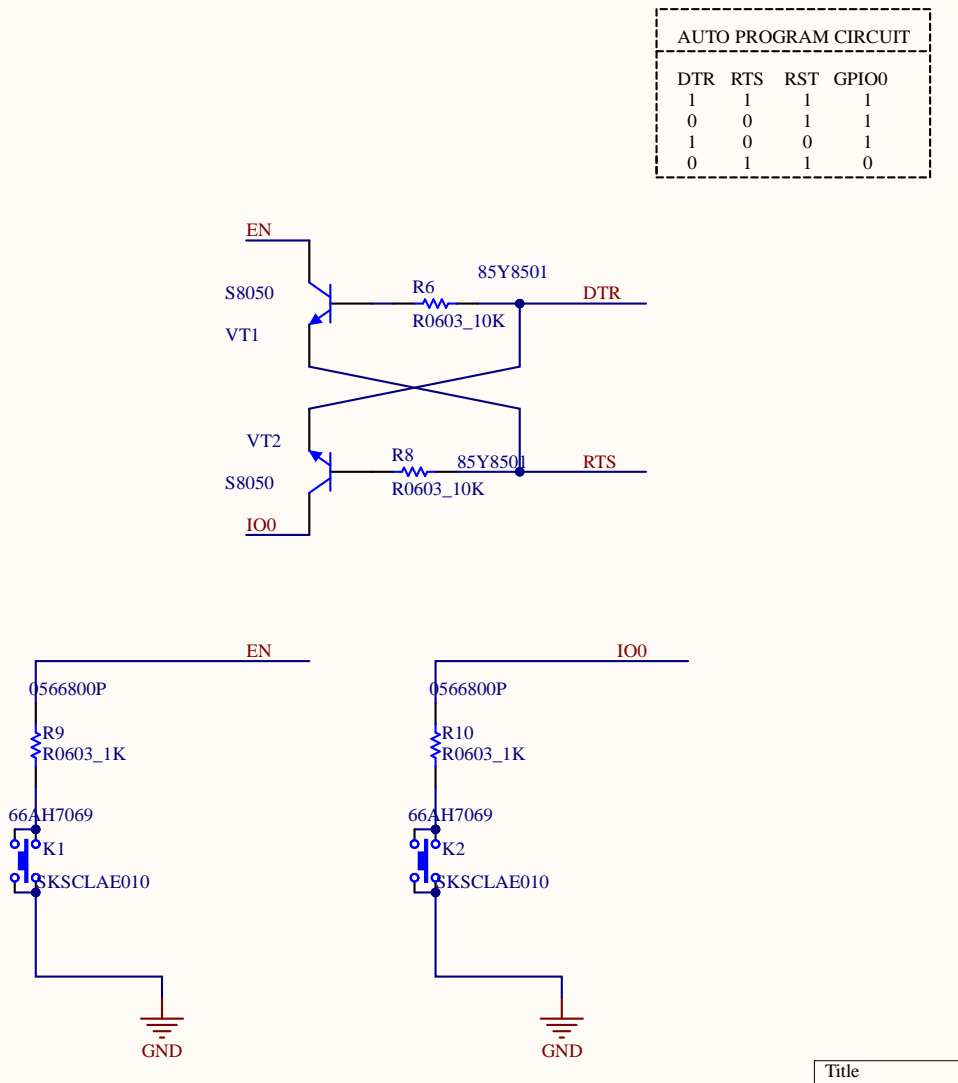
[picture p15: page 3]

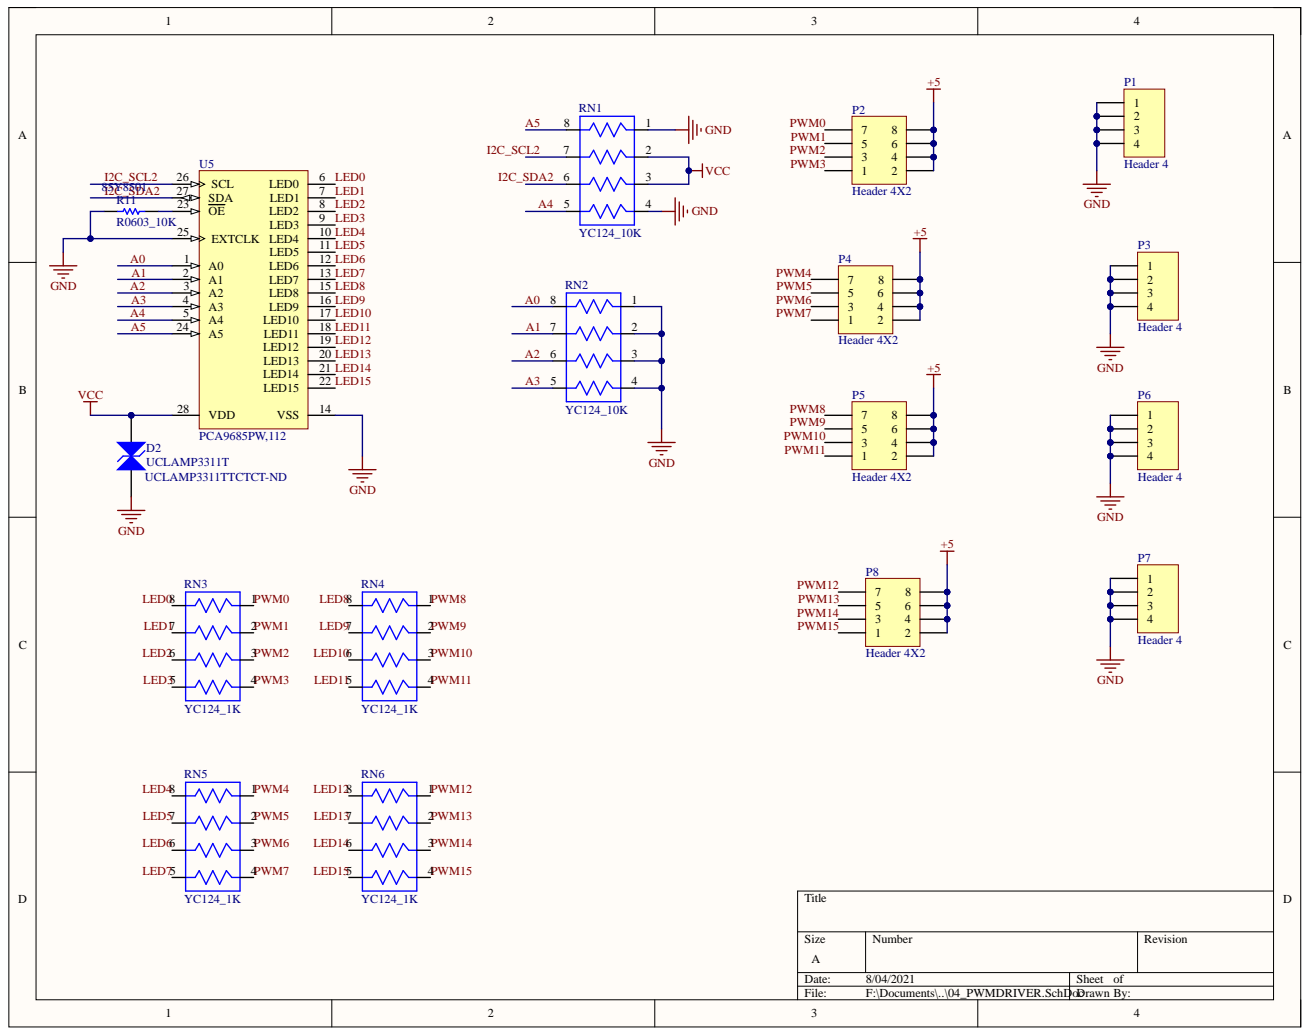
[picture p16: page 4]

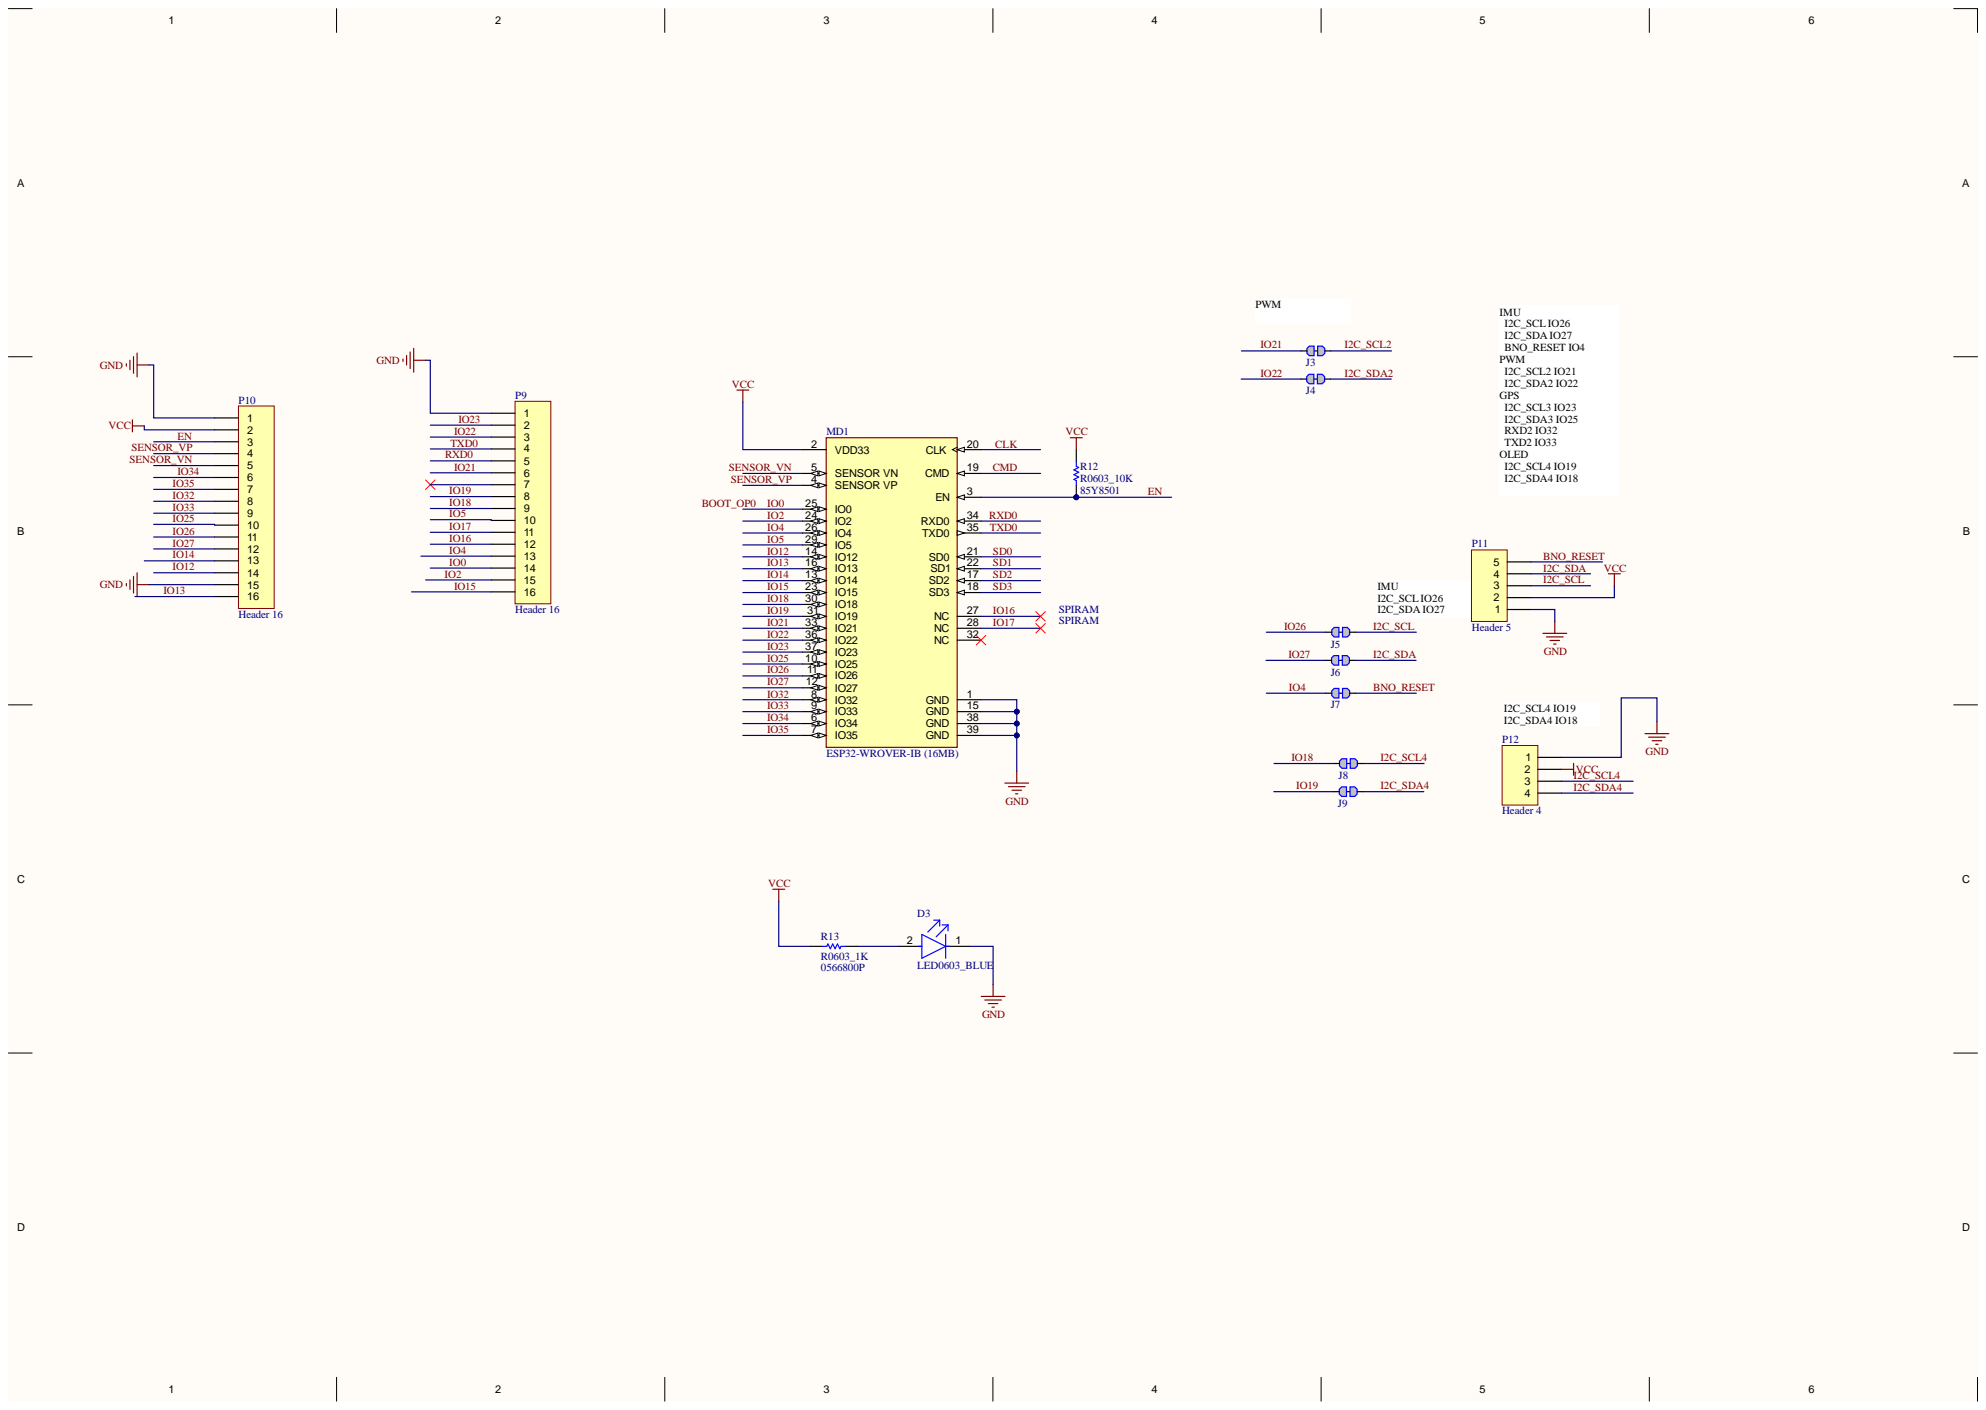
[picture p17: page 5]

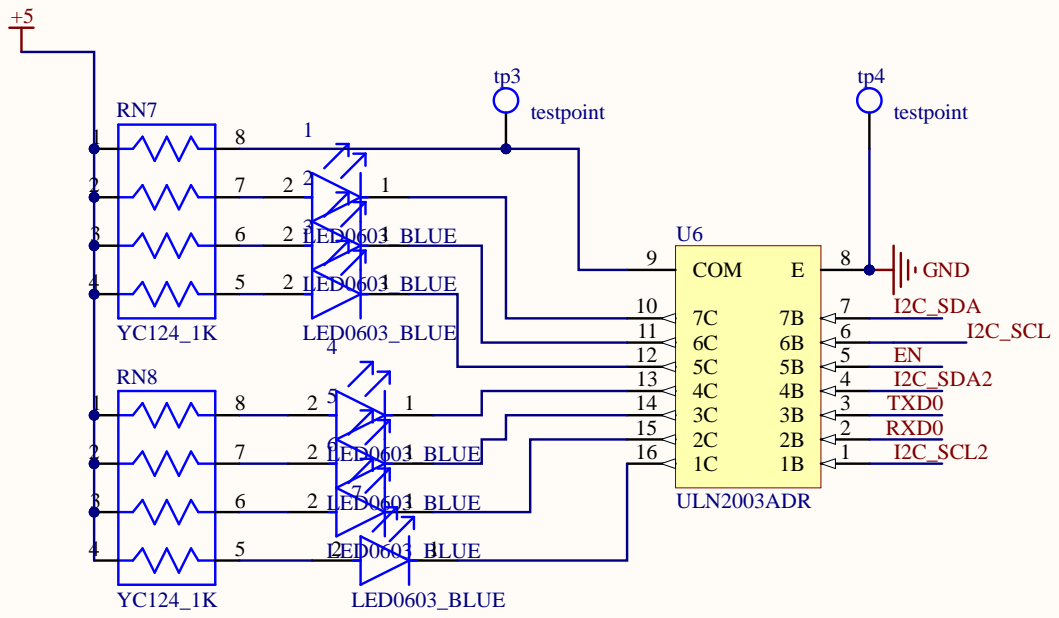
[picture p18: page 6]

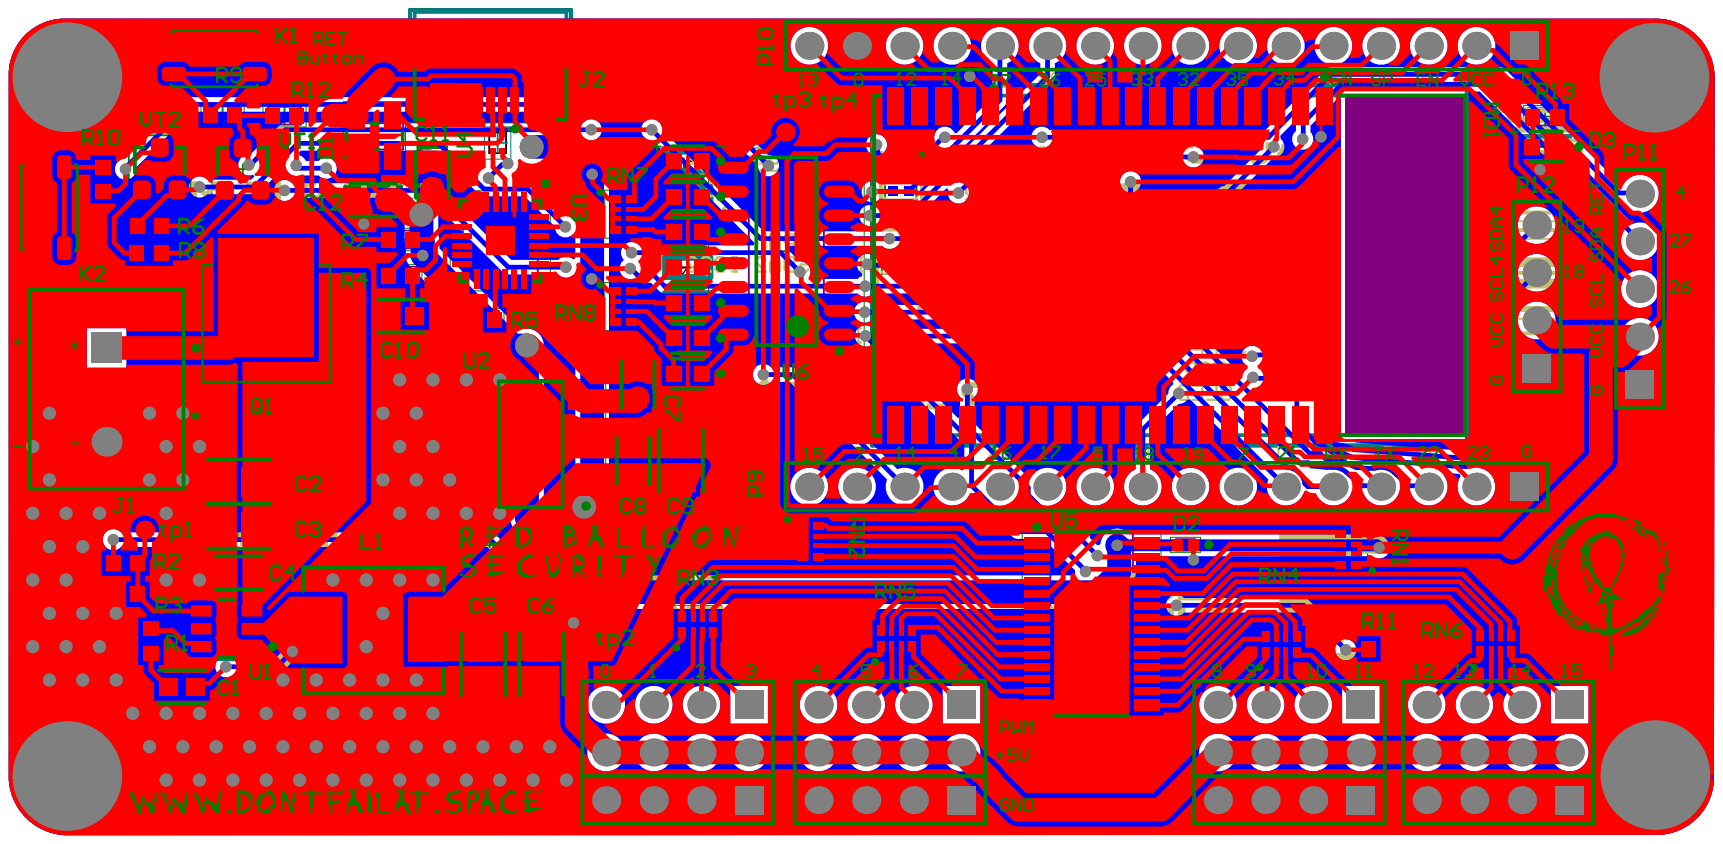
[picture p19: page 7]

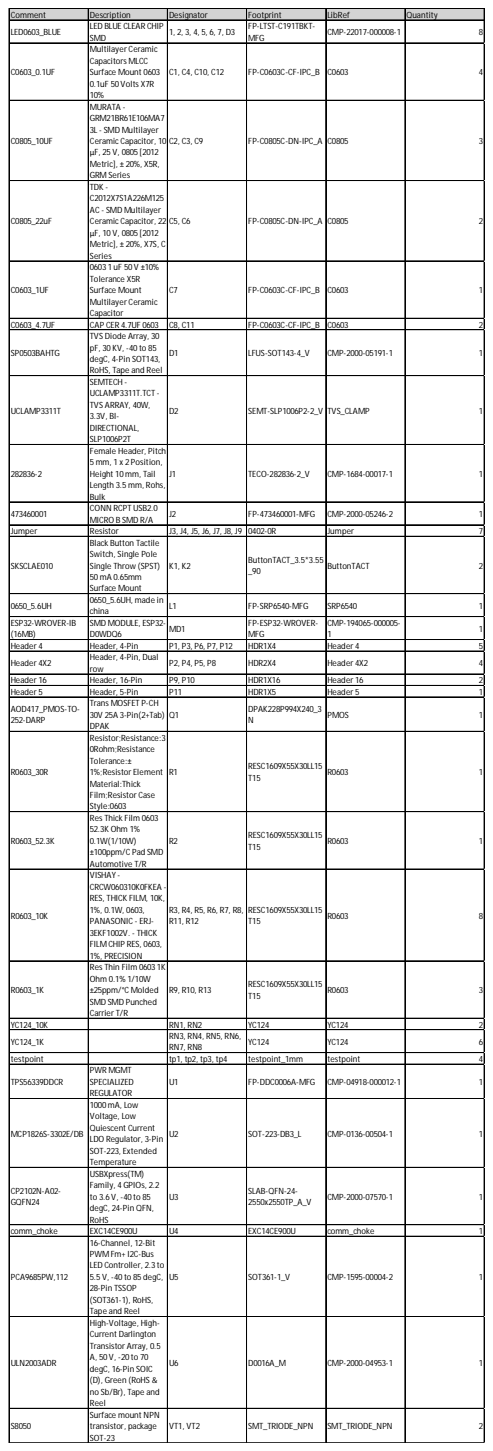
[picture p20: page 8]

Comment | Description | Designator | Footprint | LibRef | Quantity
LED0603_BLUE | LED BLUE CLEAR CHIP SMD | 1, 2, 3, 4, 5, 6, 7, D3 | FP-LTST-C191TBKT-MFG | CMP-22017-000008-1 | | 8

C0603_0.1UF | Multilayer Ceramic Capacitors MLCC Surface Mount 0603 0.1uF 50 Volts X7R 10% | C1, C4, C10, C12 | FP-C0603C-CF-IPC_B | C0603 | | 4

C0805_10UF | MURATA -GRM21BR61E106MA7 3L - SMD Multilayer Ceramic Capacitor, 10 µF, 25 V, 0805 [2012 Metric], ± 20%, X5R, GRM Series | C2, C3, C9 | FP-C0805C-DN-IPC_A | C0805 | | 3

C0805_22uF | TDK -C2012X7S1A226M125 AC - SMD Multilayer Ceramic Capacitor, 22 µF, 10 V, 0805 [2012 Metric], ± 20%, X7S, C Series | C5, C6 | FP-C0805C-DN-IPC_A | C0805 | | 2

C0603_1UF | 0603 1 uF 50 V ±10% Tolerance X5R Surface Mount Multilayer Ceramic Capacitor | C7 | FP-C0603C-CF-IPC_B | C0603 | | 1

C0603_4.7UF | CAP CER 4.7UF 0603 | C8, C11 | FP-C0603C-CF-IPC_B | C0603 | | 2
SP0503BAHTG | TVS Diode Array, 30 pF, 30 KV, -40 to 85 degC, 4-Pin SOT143, RoHS, Tape and Reel | D1 | LFUS-SOT143-4_V | CMP-2000-05191-1 | | 1

UCLAMP3311T | SEMTECH -UCLAMP3311T.TCT -TVS ARRAY, 40W, 3.3V, BI-DIRECTIONAL, SLP1006P2T | D2 | SEMT-SLP1006P2-2_V | TVS_CLAMP | | 1

282836-2 | Female Header, Pitch 5mm, 1 x 2 Position, Height 10mm, Tail Length 3.5mm, Rohs, Bulk | J1 | TECO-282836-2_V | CMP-1684-00017-1 | | 1

473460001 | CONN RCPT USB2.0 MICRO B SMD R/A | J2 | FP-473460001-MFG | CMP-2000-05246-2 | | 1

Jumper | Resistor | J3, J4, J5, J6, J7, J8, J9 | 0402-0R | Jumper | | 7
SKSCLAE010 | Black Button Tactile Switch, Single Pole Single Throw (SPST) 50mA 0.65mm Surface Mount | K1, K2 | ButtonTACT_3.5*3.55 _90 | ButtonTACT | | 2

0650_5.6UH | 0650_5.6UH, made in china | L1 | FP-SRP6540-MFG | SRP6540 | | 1

ESP32-WROVER-IB (16MB) | SMD MODULE, ESP32-D0WDQ6 | MD1 | FP-ESP32-WROVER-MFG | CMP-194065-000005-1 | | 1

Header 4 | Header, 4-Pin | P1, P3, P6, P7, P12 | HDR1X4 | Header 4 | | 5
Header 4X2 | Header, 4-Pin, Dual row | P2, P4, P5, P8 | HDR2X4 | Header 4X2 | | 4

Header 16 | Header, 16-Pin | P9, P10 | HDR1X16 | Header 16 | | 2
Header 5 | Header, 5-Pin | P11 | HDR1X5 | Header 5 | | 1
AOD417_PMOS-TO-252-DARP | Trans MOSFET P-CH 30V 25A 3-Pin(2+Tab) DPAK | Q1 | DPAK228P994X240_3 N | PMOS | | 1

R0603_30R | Resistor;Resistance:3 0Rohm;Resistance Tolerance:± 1%;Resistor Element Material:Thick Film;Resistor Case Style:0603 | R1 | RESC1609X55X30LL15 T15 | R0603 | | 1

R0603_52.3K | Res Thick Film 0603 52.3K Ohm 1% 0.1W(1/10W) ±100ppm/C Pad SMD Automotive T/R | R2 | RESC1609X55X30LL15 T15 | R0603 | | 1

R0603_10K | VISHAY -CRCW060310K0FKEA -RES, THICK FILM, 10K, 1%, 0.1W, 0603, PANASONIC - ERJ-3EKF1002V. - THICK FILM CHIP RES, 0603, 1%, PRECISION | R3, R4, R5, R6, R7, R8, R11, R12 | RESC1609X55X30LL15 T15 | R0603 | | 8

R0603_1K | Res Thin Film 0603 1K Ohm 0.1% 1/10W ±25ppm/°C Molded SMD SMD Punched Carrier T/R | R9, R10, R13 | RESC1609X55X30LL15 T15 | R0603 | | 3

YC124_10K | | RN1, RN2 | YC124 | YC124 | | 2
YC124_1K | | RN3, RN4, RN5, RN6, RN7, RN8 | YC124 | YC124 | | 6

testpoint | | tp1, tp2, tp3, tp4 | testpoint_1mm | testpoint | | 4
TPS56339DDCR | PWR MGMT SPECIALIZED REGULATOR | U1 | FP-DDC0006A-MFG | CMP-04918-000012-1 | | 1

MCP1826S-3302E/DB | 1000mA, Low Voltage, Low Quiescent Current LDO Regulator, 3-Pin SOT-223, Extended Temperature | U2 | SOT-223-DB3_L | CMP-0136-00504-1 | | 1

CP2102N-A02-GQFN24 | USBXpress(TM) Family, 4 GPIOs, 2.2 to 3.6 V, -40 to 85 degC, 24-Pin QFN, RoHS | U3 | SLAB-QFN-24-2550x2550TP_A_V | CMP-2000-07570-1 | | 1

comm_choke | EXC14CE900U | U4 | EXC14CE900U | comm_choke | | 1
PCA9685PW,112 | 16-Channel, 12-Bit PWM Fm+ I2C-Bus LED Controller, 2.3 to 5.5 V, -40 to 85 degC, 28-Pin TSSOP (SOT361-1), RoHS, Tape and Reel | U5 | SOT361-1_V | CMP-1595-00004-2 | | 1

ULN2003ADR | High-Voltage, High-Current Darlington Transistor Array, 0.5 A, 50 V, -20 to 70 degC, 16-Pin SOIC (D), Green (RoHS & no Sb/Br), Tape and Reel | U6 | D0016A_M | CMP-2000-04953-1 | | 1

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

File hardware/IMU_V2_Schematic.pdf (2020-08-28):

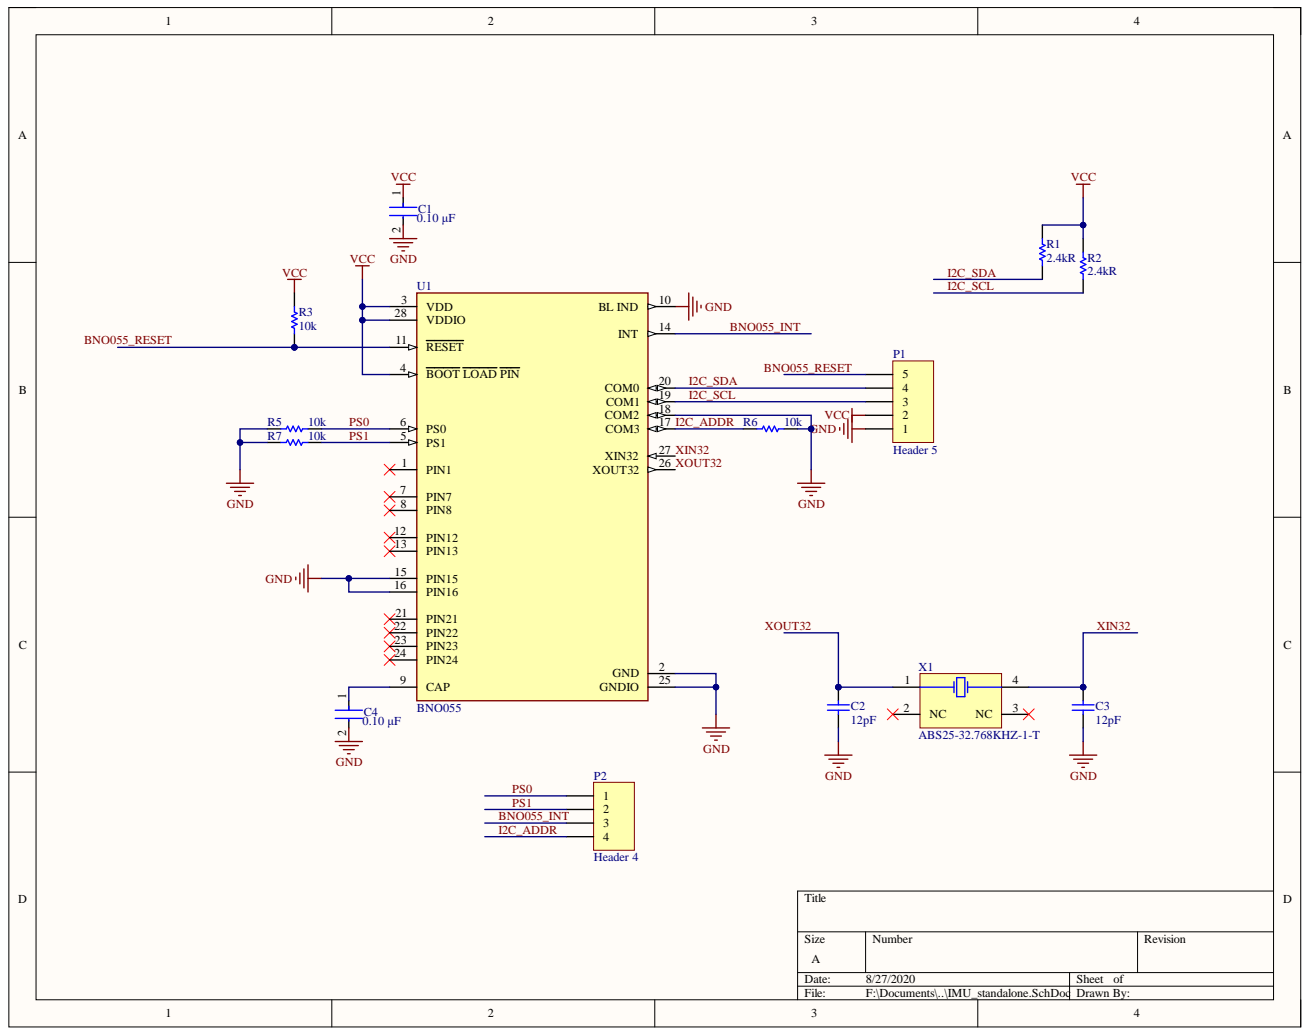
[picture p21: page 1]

VDDIO 28

RESET 11 BOOT LOAD PIN 4

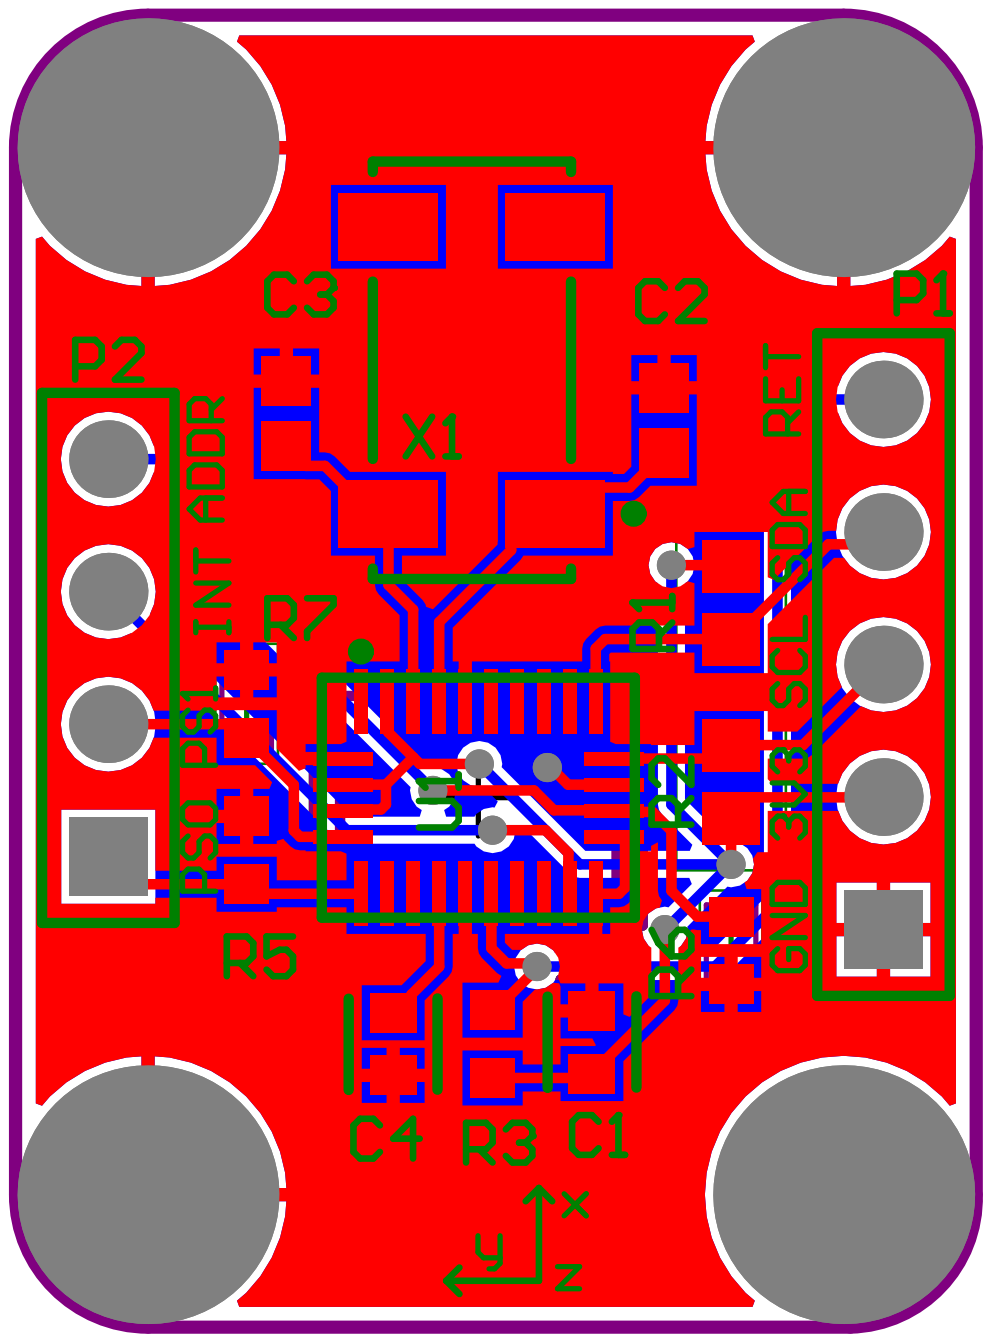
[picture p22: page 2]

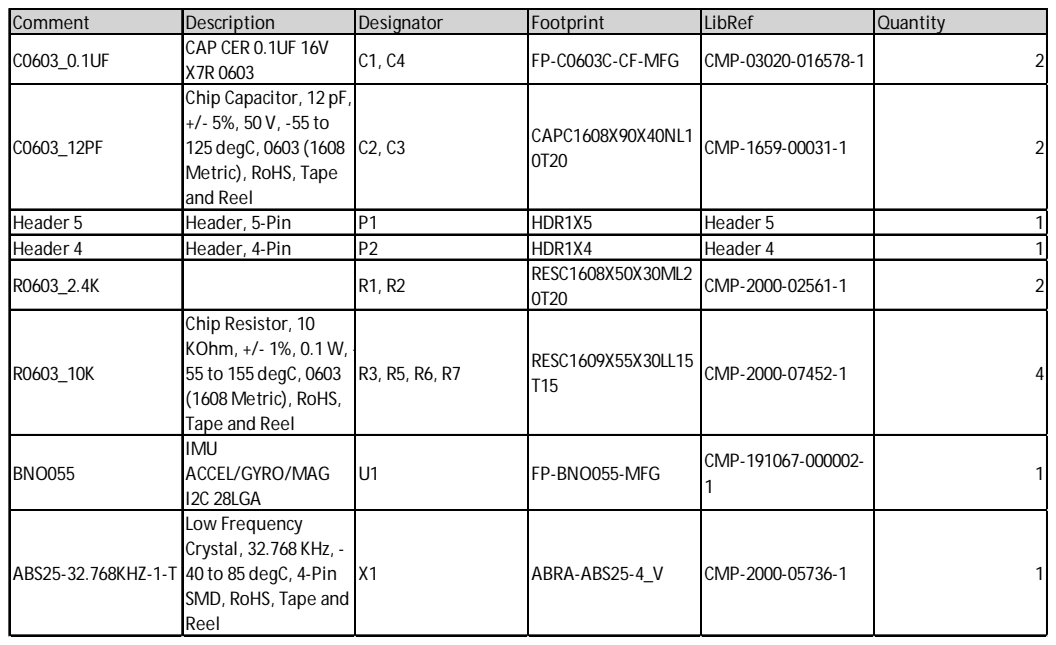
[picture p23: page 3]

Comment | Description | Designator | Footprint | LibRef | Quantity
C0603_0.1UF | CAP CER 0.1UF 16V X7R 0603 | C1, C4 | FP-C0603C-CF-MFG | CMP-03020-016578-1 | 2

C0603_12PF | Chip Capacitor, 12 pF, +/- 5%, 50 V, -55 to 125 degC, 0603 (1608 Metric), RoHS, Tape and Reel | C2, C3 | CAPC1608X90X40NL1 0T20 | CMP-1659-00031-1 | 2

Header 5 | Header, 5-Pin | P1 | HDR1X5 | Header 5 | 1
Header 4 | Header, 4-Pin | P2 | HDR1X4 | Header 4 | 1
R0603_2.4K | | R1, R2 | RESC1608X50X30ML2 0T20 | CMP-2000-02561-1 | 2

R0603_10K | Chip Resistor, 10 KOhm, +/- 1%, 0.1 W, -55 to 155 degC, 0603 (1608 Metric), RoHS, Tape and Reel | R3, R5, R6, R7 | RESC1609X55X30LL15 T15 | CMP-2000-07452-1 | 4

BNO055 | IMU ACCEL/GYRO/MAG I2C 28LGA | U1 | FP-BNO055-MFG | CMP-191067-000002-1 | 1

ABS25-32.768KHZ-1-T | Low Frequency Crystal, 32.768 KHz, -40 to 85 degC, 4-Pin SMD, RoHS, Tape and Reel | X1 | ABRA-ABS25-4_V | CMP-2000-05736-1 | 1

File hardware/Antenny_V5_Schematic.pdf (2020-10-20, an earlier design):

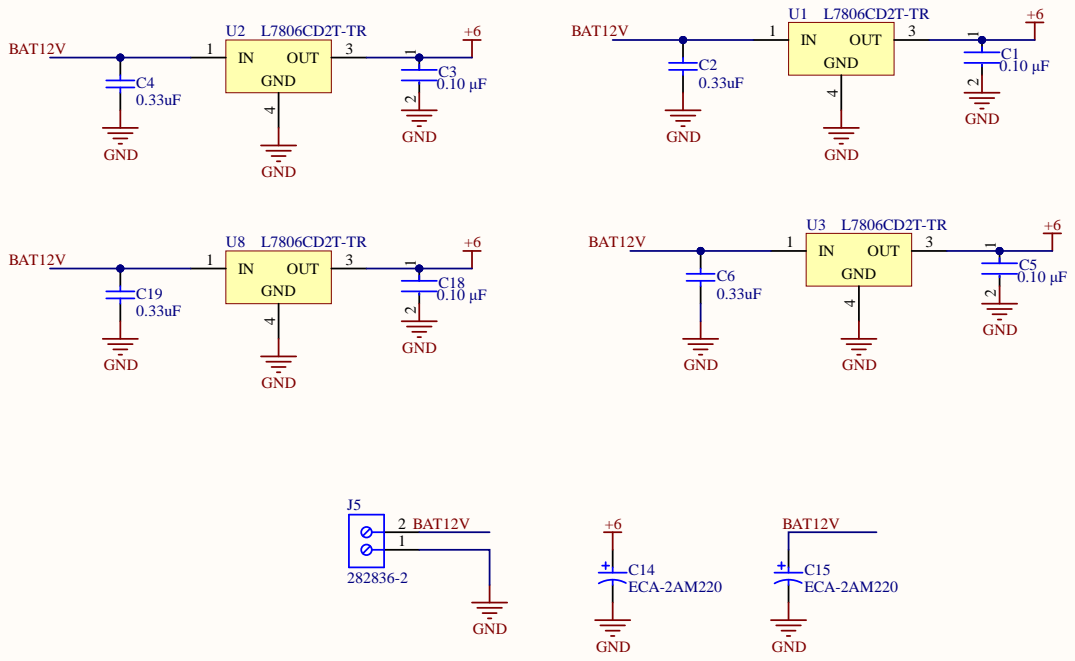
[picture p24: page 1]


GND 5
SHLD1 6

SHLD3 8

Letter
F:\Documents\antenny\hardware\Antenna_base_v5\02_USB2UART.SchDoc








F:\Documents\antenny\hardware\Antenna_base_v5\13_LED_Array.SchDoc



Comment | Description | Designator | Footprint | LibRef | Quantity
C0603_0.1UF | CAP CER 0.1UF 16V X7R 0603 | C1, C3, C5, C9, C10, C12, C13, C18, C25, C26 | FP-C0603C-CF-MFG | CMP-03020-016578-1 | 10

C0603_0.33UF | Chip Capacitor, 0.33 uF, +/- 10%, 50 V, -55 to 125 degC, 0603 (1608 Metric), RoHS, Tape and Reel | C2, C4, C6, C19 | CAPC1608X90X20LL10 CMP-2000-07551-1 | | 4

C0603_1UF | | C7, C8, C11, C22, C23 | CAPC1608X87X35LL15 T15 | CMP-2006-03318-1 | 5

ECA-2AM220 | Aluminum Electrolytic Capacitor, 22 uF, +/-20%, 100 V, -40 to 85 degC, 2-Pin THD, RoHS, Bulk | C14, C15 | CAPPR55-250-1120X630X1220 | CMP-1665-00035-2 | 2

C0805_10UF | | C24, C29 | CAPC2013X135X50LL1 0T20 | CMP-2007-03453-1 | 2

DIODE_1N5819 | DIODE SCHOTTKY 40V 1A SOD123 | D1, D2, D3, D5, D6, D7 | FP-SOD123-MFG | CMP-12790-000018-1 | 6

LED0603_BLUE | LED BLUE CLEAR CHIP SMD | D4, D9, D10, D11, D12, D13, D14, D15, D16, D17, D18, D19, D20, D21, D22, D23, D24, D25, D26, D27, D28, D29, D30, D31, D32, D33, D34, D35, D36 | FP-LTST-C191TBKT-MFG | CMP-22017-000008-1 | 29

LED | LED GREEN CLEAR CHIP SMD | D8 | FP-LTST-C190GKT-MFG | CMP-22017-000005-1 | 1

47346-0001 | Micro-USB B Receptacle with Flange, -30 to 85 degC, 5-Pin SMD, RoHS, Tape and Reel | J1 | MOLX-47346-0001-5_V | CMP-2000-05246-1 | 1

282836-2 | Female Header, Pitch 5mm, 1 x 2 Position, Height 10mm, Tail Length 3.5mm, Rohs, Bulk | J5 | TECO-282836-2_V | CMP-1684-00017-1 | 1

ESP32-WROOM-32D | WIFI MODULE 32MBITS SPI FLASH | MD1 | FP-ESP32-WROOM-32D-MFG | CMP-194065-000003-1 | 1

Header 4 | Header, 4-Pin | P1, P3 | HDR1X4 | Header 4 | 2
Header 5 | Header, 5-Pin | P2 | HDR1X5 | Header 5 | 1
Header 6 | Header, 6-Pin | P4 | HDR1X6 | Header 6 | 1
Header 16 | Header, 16-Pin | P5, P6, P7 | HDR1X16 | Header 16 | 3
Header 6X2 | Header, 6-Pin, Dual row | P8 | HDR2X6 | Header 6X2 | 1

Header 2 | Header, 2-Pin | P9, P10, P11 | HDR1X2 | Header 2 | 3
BCP56-16 | TRANS NPN 80V 1A SOT-223 | Q1, Q2 | FP-SOT-223-P008-MFG | CMP-12195-000003-1 | 2

R0603_10K | Chip Resistor, 10 KOhm, +/- 1%, 0.1 W, -55 to 155 degC, 0603 (1608 Metric), RoHS, Tape and Reel | R1, R2, R3, R4, R6, R7, R12, R13, R14, R15, R16, R17, R18, R19, R20, R21, R24, R25, R26, R27, R28, R29, R30, R31, R32, R33, R45, R48, R49, R63 | RESC1609X55X30LL15 T15 | CMP-2000-07452-1 | 30

R0603_4.7K | Resistor | R5, R44 | J1-0603 | Res3 | 2
R0603_120R | | R8, R9, R10, R11, R43 | RESC1608X55X30NL20 T20 | CMP-2000-00896-1 | 5

R0603_2.4K | | R22, R23 | RESC1608X50X30ML2 0T20 | CMP-2000-02561-1 | 2

R0603_470R | | R34, R35, R36, R37, R38, R39, R40, R41, R42, R46, R47, R50, R51, R52, R53, R54, R55, R56, R57, R58, R59, R60, R61, R62, R64, R65, R66, R67, R68 | RESC1608X55X30NL15 T15 | CMP-2000-00795-1 | 29

push_button | FSMSM Push Button Switch, 50mA, -35 to 85 degC, 2-Pin SMD, RoHS, Tape and Reel | SW1, SW2 | TECO-FSMSMTR_V | CMP-2000-07501-1 | 2

L7806CD2T-TR | Positive Voltage Regulator, 3-Pin D2PAK, Tape and Reel | U1, U2, U3, U8 | TO-263_L | CMP-0244-00208-1 | 4

MCP1826S-3302E/DB | 1000mA, Low Voltage, Low Quiescent Current LDO Regulator, 3-Pin SOT-223, Extended Temperature | U4 | SOT-223-DB3_L | CMP-0136-00504-1 | 1

CP2102N-A01-GQFN24 | USBXpress(TM) Family, 4 GPIOs, 2.2 to 3.6 V, -40 to 85 degC, 24-Pin QFN, RoHS | U5 | SLAB-QFN-24-2550x2550TP_A_V | CMP-2000-07570-1 | 1

ULN2803ADWR | Darlington Transistor Array, -40 to 85 degC, 18-Pin SOIC (DW), Green (RoHS & no Sb/Br), Tape and Reel | U6, U9, U10 | DW0018A_L | CMP-2000-07354-1 | 3

PCA9685PW | 16-Channel, 12-Bit PWM Fm+ I2C-Bus LED Controller, 2.3 to 5.5 V, -40 to 85 degC, 28-Pin TSSOP (SOT361-1), RoHS, Tape and Reel | U7 | SOT361-1_V | CMP-1595-00004-2 | 1

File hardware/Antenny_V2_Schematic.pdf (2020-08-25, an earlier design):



GND 5
SHLD1 6

SHLD3 8

Letter
F:\Documents\antenny\hardware\Antenna_base_v2\02_USB2UART.SchDoc



R24 | 8
10k | | 9 I2C_SCL 2


F:\Documents\antenny\hardware\Antenna_base_v2\08_CoreBoard.SchDoc





Comment | Description | Designator | Footprint | LibRef | Quantity
C0603_0.1UF | CAP CER 0.1UF 16V X7R 0603 | C1, C3, C5, C9, C10, C12, C13, C18, C25, C26 | FP-C0603C-CF-MFG | CMP-03020-016578-1 | 10

C0603_0.33UF | Chip Capacitor, 0.33 uF, +/- 10%, 50 V, -55 to 125 degC, 0603 (1608 Metric), RoHS, Tape and Reel | C2, C4, C6, C19 | CAPC1608X90X20LL10 CMP-2000-07551-1 | | 4

C0603_1UF | | C7, C8, C11, C22, C23 | CAPC1608X87X35LL15 T15 | CMP-2006-03318-1 | 5

C0805_10UF | | C24, C29 | CAPC2013X135X50LL1 0T20 | CMP-2007-03453-1 | 2

CC0603JRNPO9BN120 | Chip Capacitor, 12 pF, +/- 5%, 50 V, -55 to 125 degC, 0603 (1608 Metric), RoHS, Tape and Reel | C27, C28 | CAPC1608X90X40NL1 0T20 | CMP-1659-00031-1 | 2

DIODE_1N5819 | DIODE SCHOTTKY 40V 1A SOD123 | D1, D2, D3, D5, D6, D7 | FP-SOD123-MFG | CMP-12790-000018-1 | 6

LED | LED GREEN CLEAR CHIP SMD | D8 | FP-LTST-C190GKT-MFG | CMP-22017-000005-1 | 1

47346-0001 | Micro-USB B Receptacle with Flange, -30 to 85 degC, 5-Pin SMD, RoHS, Tape and Reel | J1 | MOLX-47346-0001-5_V | CMP-2000-05246-1 | 1

282836-2 | Female Header, Pitch 5mm, 1 x 2 Position, Height 10mm, Tail Length 3.5mm, Rohs, Bulk | J5 | TECO-282836-2_V | CMP-1684-00017-1 | 1

ESP32-WROOM-32D | WIFI MODULE 32MBITS SPI FLASH | MD1 | FP-ESP32-WROOM-32D-MFG | CMP-194065-000003-1 | 1

Header 4 | Header, 4-Pin | P1, P2, P3 | HDR1X4 | Header 4 | 3
Header 6 | Header, 6-Pin | P4 | HDR1X6 | Header 6 | 1
Header 16 | Header, 16-Pin | P5, P6, P7 | HDR1X16 | Header 16 | 3
Header 13X2 | Header, 13-Pin, Dual row | P8 | HDR2X13 | Header 13X2 | 1

BCP56-16 | TRANS NPN 80V 1A SOT-223 | Q1, Q2 | FP-SOT-223-P008-MFG | CMP-12195-000003-1 | 2

R0603_10K | Chip Resistor, 10 KOhm, +/- 1%, 0.1 W, -55 to 155 degC, 0603 (1608 Metric), RoHS, Tape and Reel | R1, R6, R7, R24, R45 | RESC1609X55X30LL15 T15 | CMP-2000-07452-1 | 5

R0603_4.7K | Resistor | R5, R44 | J1-0603 | Res3 | 2
R0603_120R | | R8, R9, R10, R11, R43 | RESC1608X55X30NL20 T20 | CMP-2000-00896-1 | 5

R0603_2.4K | | R22, R23 | RESC1608X50X30ML2 0T20 | CMP-2000-02561-1 | 2

push_button | FSMSM Push Button Switch, 50mA, -35 to 85 degC, 2-Pin SMD, RoHS, Tape and Reel | SW1, SW2 | TECO-FSMSMTR_V | CMP-2000-07501-1 | 2

L7806CD2T-TR | Positive Voltage Regulator, 3-Pin D2PAK, Tape and Reel | U1, U2, U3, U8 | TO-263_L | CMP-0244-00208-1 | 4

MCP1826S-3302E/DB | 1000mA, Low Voltage, Low Quiescent Current LDO Regulator, 3-Pin SOT-223, Extended Temperature | U4 | SOT-223-DB3_L | CMP-0136-00504-1 | 1

CP2102N-A01-GQFN24 | USBXpress(TM) Family, 4 GPIOs, 2.2 to 3.6 V, -40 to 85 degC, 24-Pin QFN, RoHS | U5 | SLAB-QFN-24-2550x2550TP_A_V | CMP-2000-07570-1 | 1

PCA9685PW | 16-Channel, 12-Bit PWM Fm+ I2C-Bus LED Controller, 2.3 to 5.5 V, -40 to 85 degC, 28-Pin TSSOP (SOT361-1), RoHS, Tape and Reel | U7 | SOT361-1_V | CMP-1595-00004-2 | 1

ABS25-32.768KHZ-1-T | Low Frequency Crystal, 32.768 KHz, -40 to 85 degC, 4-Pin SMD, RoHS, Tape and Reel | X1 | ABRA-ABS25-4_V | CMP-2000-05736-1 | 1

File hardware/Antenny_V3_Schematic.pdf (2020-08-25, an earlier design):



GND 5
SHLD1 6

SHLD3 8

Letter
F:\Documents\antenny\hardware\Antenna_base_v3\02_USB2UART.SchDoc



R24 | 8
10k | | 9 I2C_SCL 2


F:\Documents\antenny\hardware\Antenna_base_v3\08_CoreBoard.SchDoc





Comment | Description | Designator | Footprint | LibRef | Quantity
C0603_0.1UF | CAP CER 0.1UF 16V X7R 0603 | C1, C3, C5, C9, C10, C12, C13, C18, C25, C26 | FP-C0603C-CF-MFG | CMP-03020-016578-1 | 10

C0603_0.33UF | Chip Capacitor, 0.33 uF, +/- 10%, 50 V, -55 to 125 degC, 0603 (1608 Metric), RoHS, Tape and Reel | C2, C4, C6, C19 | CAPC1608X90X20LL10 CMP-2000-07551-1 | | 4

C0603_1UF | | C7, C8, C11, C22, C23 | CAPC1608X87X35LL15 T15 | CMP-2006-03318-1 | 5

ECA-2AM220 | Aluminum Electrolytic Capacitor, 22 uF, +/-20%, 100 V, -40 to 85 degC, 2-Pin THD, RoHS, Bulk | C14, C15 | CAPPR55-250-1120X630X1220 | CMP-1665-00035-2 | 2

C0805_10UF | | C24, C29 | CAPC2013X135X50LL1 0T20 | CMP-2007-03453-1 | 2

CC0603JRNPO9BN120 | Chip Capacitor, 12 pF, +/- 5%, 50 V, -55 to 125 degC, 0603 (1608 Metric), RoHS, Tape and Reel | C27, C28 | CAPC1608X90X40NL1 0T20 | CMP-1659-00031-1 | 2

DIODE_1N5819 | DIODE SCHOTTKY 40V 1A SOD123 | D1, D2, D3, D5, D6, D7 | FP-SOD123-MFG | CMP-12790-000018-1 | 6

LED | LED GREEN CLEAR CHIP SMD | D8 | FP-LTST-C190GKT-MFG | CMP-22017-000005-1 | 1

47346-0001 | Micro-USB B Receptacle with Flange, -30 to 85 degC, 5-Pin SMD, RoHS, Tape and Reel | J1 | MOLX-47346-0001-5_V | CMP-2000-05246-1 | 1

282836-2 | Female Header, Pitch 5mm, 1 x 2 Position, Height 10mm, Tail Length 3.5mm, Rohs, Bulk | J5 | TECO-282836-2_V | CMP-1684-00017-1 | 1

ESP32-WROOM-32D | WIFI MODULE 32MBITS SPI FLASH | MD1 | FP-ESP32-WROOM-32D-MFG | CMP-194065-000003-1 | 1

Header 4 | Header, 4-Pin | P1, P2, P3 | HDR1X4 | Header 4 | 3
Header 6 | Header, 6-Pin | P4 | HDR1X6 | Header 6 | 1
Header 16 | Header, 16-Pin | P5, P6, P7 | HDR1X16 | Header 16 | 3
Header 13X2 | Header, 13-Pin, Dual row | P8 | HDR2X13 | Header 13X2 | 1

BCP56-16 | TRANS NPN 80V 1A SOT-223 | Q1, Q2 | FP-SOT-223-P008-MFG | CMP-12195-000003-1 | 2

R0603_10K | Chip Resistor, 10 KOhm, +/- 1%, 0.1 W, -55 to 155 degC, 0603 (1608 Metric), RoHS, Tape and Reel | R1, R2, R3, R4, R6, R7, R12, R13, R14, R15, R16, R17, R18, R19, R20, R21, R24, R25, R26, R27, R45 | RESC1609X55X30LL15 T15 | CMP-2000-07452-1 | 21

R0603_4.7K | Resistor | R5, R44 | J1-0603 | Res3 | 2
R0603_120R | | R8, R9, R10, R11, R43 | RESC1608X55X30NL20 T20 | CMP-2000-00896-1 | 5

R0603_2.4K | | R22, R23 | RESC1608X50X30ML2 0T20 | CMP-2000-02561-1 | 2

push_button | FSMSM Push Button Switch, 50mA, -35 to 85 degC, 2-Pin SMD, RoHS, Tape and Reel | SW1, SW2 | TECO-FSMSMTR_V | CMP-2000-07501-1 | 2

L7806CD2T-TR | Positive Voltage Regulator, 3-Pin D2PAK, Tape and Reel | U1, U2, U3, U8 | TO-263_L | CMP-0244-00208-1 | 4

MCP1826S-3302E/DB | 1000mA, Low Voltage, Low Quiescent Current LDO Regulator, 3-Pin SOT-223, Extended Temperature | U4 | SOT-223-DB3_L | CMP-0136-00504-1 | 1

CP2102N-A01-GQFN24 | USBXpress(TM) Family, 4 GPIOs, 2.2 to 3.6 V, -40 to 85 degC, 24-Pin QFN, RoHS | U5 | SLAB-QFN-24-2550x2550TP_A_V | CMP-2000-07570-1 | 1

PCA9685PW | 16-Channel, 12-Bit PWM Fm+ I2C-Bus LED Controller, 2.3 to 5.5 V, -40 to 85 degC, 28-Pin TSSOP (SOT361-1), RoHS, Tape and Reel | U7 | SOT361-1_V | CMP-1595-00004-2 | 1

ABS25-32.768KHZ-1-T | Low Frequency Crystal, 32.768 KHz, -40 to 85 degC, 4-Pin SMD, RoHS, Tape and Reel | X1 | ABRA-ABS25-4_V | CMP-2000-05736-1 | 1

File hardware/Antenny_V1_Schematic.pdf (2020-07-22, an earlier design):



GND 5 SHLD1 6 SHLD2 7




R24 | 8
10k | | 9 I2C_SCL 2






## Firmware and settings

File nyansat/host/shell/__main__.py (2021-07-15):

import argparse
import io
import logging
import platform
import sys
from websocket import WebSocketConnectionClosedException

import serial
from mp import mpfshell

from nyansat.host.shell.cli_arg_parser import CLIArgumentProperty, parse_cli_args
from nyansat.host.shell.terminal_printer import TerminalPrinter
from nyansat.host.shell.antenny_client import AntennyClient

from nyansat.host.shell.errors import cli_handler


class NyanShell(mpfshell.MpFileShell):
    """Extension of MPFShell that adds NyanSat-specific features"""

    def __init__(self, color=False, caching=False, reset=False):
        """Creates Cmd-based shell object.

        Keyword arguments:
        color -- support colored text in the shell
        caching -- support caching the results of functions like 'ls'
        reset -- hard reset device via DTR. (serial connection only)
        """
        super().__init__(color, caching, reset)

        self.client = AntennyClient(self.caching)
        self._intro()
        self._set_prompt_path()
        self.emptyline = lambda: None

    def _intro(self):
        self.intro = TerminalPrinter.intro()

    def _disconnect(self):
        return super()._MpFileShell__disconnect()

    def _connect(self, port):
        """
        Creates FileExplorers. Also creates a AntennyClient (which creates an invoker) using
        FileExplorer's self.con object.
        """
        super()._MpFileShell__connect(port)
        self._set_prompt_path()
        self.client.initialize(self.fe)

    def _set_prompt_path(self):
        """Prompt that appears at the beginning of every line in the shell."""
        if self.fe is not None:
            pwd = self.fe.pwd()
        else:
            pwd = "/"
        self.prompt = TerminalPrinter.prompt(pwd)

    def do_open(self, args):
        """open <TARGET>
        Open connection to device with given target. TARGET might be:
        - a serial port, e.g.       ttyUSB0, ser:/dev/ttyUSB0
        - a telnet host, e.g        tn:192.168.1.1 or tn:192.168.1.1,login,passwd
        - a websocket host, e.g.    ws:192.168.1.1 or ws:192.168.1.1,passwd
        """
        arg_properties = [
            CLIArgumentProperty(
                str,
                None
            )
        ]
        parsed_args = parse_cli_args(args, 'open', 1, arg_properties)
        port, = parsed_args
        if (
                port.startswith("ser:")
                or port.startswith("tn:")
                or port.startswith("ws:")
        ):
            return self._connect(args)
        else:
            if platform.system() == "Windows":
                if not port.startswith("COM"):
                    raise argparse.ArgumentError("Windows ports should start with COM")
                args = "ser:" + args
            else:
                if not port.startswith("/dev/"):
                    args = "ser:/dev/" + args
                else:
                    args = "ser:" + args

        return self._connect(args)

    def do_repl(self, args):
        self.__doc__ = super().do_repl.__doc__
        try:
            super().do_repl(args)
        except WebSocketConnectionClosedException as e:
            TerminalPrinter.print_error("Connection lost to repl")
            self._disconnect()

    @cli_handler
    def do_setup(self, args):
        """setup <CONFIG_FILE>
        Interactive script to populate a config file.
        Switches to new config after finishing setup.
        To keep config persistent after reboots, name it "config.json"
        """
        arg_properties = [
            CLIArgumentProperty(
                str,
                None
            )
        ]
        parsed_args = parse_cli_args(args, 'setup', 1, arg_properties)
        name, = parsed_args
        self.client.setup(name)

    @cli_handler
    def do_set(self, args):
        """set <CONFIG_PARAM> <NEW_VAL>
        Set a parameter in the configuration file to a new value."""
        arg_properties = [
            CLIArgumentProperty(
                str,
                None
            ),
            CLIArgumentProperty(
                str,
                None
            )
        ]
        parsed_args = parse_cli_args(args, 'set', 2, arg_properties)
        key, new_val = parsed_args
        self.client.set(key, new_val)

    def complete_set(self, *args):
        """Tab completion for 'set' command."""
        return [key for key in self.client.get_prompts().keys() if key.startswith(args[0])]

    def do_configs(self, args):
        """configs
        Print a list of all configuration parameters."""
        self.client.configs()

    @cli_handler
    def do_load(self, args):
        """switch <CONFIG_FILE>
        Switch to using a different config file."""
        arg_properties = [
            CLIArgumentProperty(
                str,
                None
            )
        ]
        parsed_args = parse_cli_args(args, 'load', 1, arg_properties)
        name, = parsed_args
        self.client.load(name)

    def do_i2ctest(self, args):
        """i2ctest
        Scan an i2c bus for i2c device addresses
        """
        self.client.i2ctest()

    def do_bnotest(self, args):
        """bnotest
        Return some diagnostic data that may be helpful in connecting a BNO055 device.
        """
        arg_properties = []
        _ = parse_cli_args(args, 'bnotest', 0, arg_properties)
        self.client.bno_test()

    def do_pwmtest(self, args):
        """pwmtest
        Return some diagnostic data that may be helpful in connecting a PCA9685 device.
        """
        arg_properties = []
        _ = parse_cli_args(args, 'pwmtest', 0, arg_properties)
        self.client.pwm_test()

    def do_calibrate(self, args):
        """calibrate
        Detect IMU calibration status and provide instructions on how to
        calibrate if necessary. If calibration is necessary, wait for the user
        to calibrate the device and cease waiting once all sensors are
        calibrated. Regardless of whether calibration is necessary or not, save
        the calibration profile to the config at the end.
        """
        arg_properties = []
        parsed_args = parse_cli_args(args, 'calibrate', 0, arg_properties)
        self.client.calibrate()

    def complete_switch(self, *args):
        """Tab completion for switch command."""
        try:
            files = self.fe.ls(add_dirs=False)
        except Exception:
            files = []
        return [f for f in files if f.startswith(args[0]) and f.endswith(".json")]

    def _calibration_wait_message(self, gyro_calibrated, accel_calibrated, magnet_calibrated, use_ellipsis=True):
        """
        generate a human-readable message that indicates which components remain
        to be calibrated, e.g. if all the arguments are true, then it should
        return the string "waiting for gyroscope, accelerometer and magnetometer
        to be calibrated...".
        """
        components = ((['gyroscope'] if not gyro_calibrated else []) +
                      (['accelerometer'] if not accel_calibrated else []) +
                      (['magnetometer'] if not magnet_calibrated else []))
        components_list_string = ', '.join(components[:-2] + [" and ".join(components[-2:])])
        if components:
            return ("waiting for " + components_list_string +
                    " to be calibrated" + ("..." if use_ellipsis else ""))
        else:
            return "all components calibrated!"

    def do_save_calibration(self, args):
        """save_calibration
        Save current IMU calibration data to the current configuration.
        """
        self.client.save_calibration()

    def do_upload_calibration(self, args):
        """upload_calibration
        Upload the currently stored calibration data to the connected IMU.
        """
        self.client.upload_calibration()

    @cli_handler
    def do_motortest(self, args):
        """motortest <EL | AZ> <ANGLE>
        Test the motors to plot their accuracy against the measured IMU values.
        """
        arg_properties = [
            CLIArgumentProperty(
                str,
                {
                    'EL', 'AZ'
                }
            ),
            CLIArgumentProperty(
                float,
                None
            )
        ]
        parsed_args = parse_cli_args(args, 'motortest', 2, arg_properties)
        motor, pos = parsed_args
        self.client.motor_test(motor, pos)

    @cli_handler
    def do_startmotion(self, args):
        """startmotion <INITIAL AZIMUTH> <INITIAL ELEVATION>
        Sets the azimuth and elevation to the provided values and enables motion.
        """
        arg_properties = [
            CLIArgumentProperty(
                float,
                None
            ),
            CLIArgumentProperty(
                float,
                None
            )
        ]
        parsed_args = parse_cli_args(args, 'startmotion', 2, arg_properties)
        az, el = parsed_args
        self.client.startmotion(az, el)

    @cli_handler
    def do_elevation(self, args):
        """elevation <ELEVATION>
        Set the elevation to the level given in degrees by the first argument.
        """
        arg_properties = [
            CLIArgumentProperty(
                float,
                None
            )
        ]
        parsed_args = parse_cli_args(args, 'elevation', 1, arg_properties)
        el, = parsed_args
        self.client.elevation(el)

    @cli_handler
    def do_azimuth(self, args):
        """azimuth <AZIMUTH>
        Set the azimuth to the level given in degrees by the first argument.
        """
        # TODO: merge this function with do_elevation in one move command

        arg_properties = [
            CLIArgumentProperty(
                float,
                None
            )
        ]
        parsed_args = parse_cli_args(args, 'azimuth', 1, arg_properties)
        az, = parsed_args
        self.client.azimuth(az)

    @cli_handler
    def do_antkontrol(self, args):
        """antkontrol <start | status>
        Create a new global AntKontrol instance or query the status of an existing one
        """
        arg_properties = [
            CLIArgumentProperty(
                str,
                {
                    'start', 'status'
                }
            )
        ]
        parsed_args = parse_cli_args(args, 'antkontrol', 1, arg_properties)
        mode, = parsed_args
        self.client.antkontrol(mode)

    @cli_handler
    def do_track(self, args):
        """track <SATELLITE_NAME>
        Tracks a satellite across the sky. Satellite data is taken from Active-Space-Stations file from Celestrak."""
        arg_properties = [
            CLIArgumentProperty(
                str,
                None
            )
        ]
        parsed_args = parse_cli_args(args, 'track', 1, arg_properties)
        sat_name, = parsed_args
        self.client.track(sat_name)

    def do_cancel(self, args):
        """cancel
        Cancel tracking mode.
        """
        self.client.cancel()

    def do_wifi(self, args):
        """wifi
        Run the WiFi setup script.
        """
        self.client.wifi_setup()


def main():
    """Entry point into the shell.
    Parse command line args and create a shell object.
    """
    parser = argparse.ArgumentParser()
    parser.add_argument(
        "-c",
        "--command",
        help="execute given commands (separated by ;)",
        default=None,
        nargs="*",
    )
    parser.add_argument(
        "-s", "--script", help="execute commands from file", default=None
    )
    parser.add_argument(
        "-n",
        "--noninteractive",
        help="non interactive mode (don't enter shell)",
        action="store_true",
        default=False,
    )

    parser.add_argument(
        "--nocolor", help="disable color", action="store_true", default=False
    )
    parser.add_argument(
        "--nocache", help="disable cache", action="store_true", default=False
    )

    parser.add_argument("--logfile", help="write log to file", default=None)
    parser.add_argument(
        "--loglevel",
        help="loglevel (CRITICAL, ERROR, WARNING, INFO, DEBUG)",
        default="INFO",
    )

    parser.add_argument(
        "--reset",
        help="hard reset device via DTR (serial connection only)",
        action="store_true",
        default=False,
    )

    parser.add_argument(
        "-o",
        "--open",
        help="directly opens board",
        metavar="BOARD",
        action="store",
        default=None,
    )
    parser.add_argument(
        "board", help="directly opens board", nargs="?", action="store", default=None
    )

    args = parser.parse_args()

    format = "%(asctime)s\t%(levelname)s\t%(message)s"

    if args.logfile is not None:
        logging.basicConfig(format=format, filename=args.logfile, level=args.loglevel)
    else:
        logging.basicConfig(format=format, level=logging.CRITICAL)

    logging.info("Micropython File Shell started")
    logging.info(
        "Running on Python %d.%d using PySerial %s"
        % (sys.version_info[0], sys.version_info[1], serial.VERSION)
    )

    nyanshell = NyanShell(not args.nocolor, not args.nocache, args.reset)

    if args.open is not None:
        if args.board is None:
            if not nyanshell.do_open(args.open):
                return 1
        else:
            print(
                "Positional argument ({}) takes precedence over --open.".format(
                    args.board
                )
            )
    if args.board is not None:
        nyanshell.do_open(args.board)

    if args.command is not None:

        for acmd in " ".join(args.command).split(";"):
            scmd = acmd.strip()
            if len(scmd) > 0 and not scmd.startswith("#"):
                nyanshell.onecmd(scmd)

    elif args.script is not None:

        f = open(args.script, "r")
        script = ""

        for line in f:

            sline = line.strip()

            if len(sline) > 0 and not sline.startswith("#"):
                script += sline + "\n"

        if sys.version_info < (3, 0):
            sys.stdin = io.StringIO(script.decode("utf-8"))
        else:
            sys.stdin = io.StringIO(script)

        nyanshell.intro = ""
        nyanshell.prompt = ""

    if not args.noninteractive:

        try:
            nyanshell.cmdloop()
        except KeyboardInterrupt:
            print("")


if __name__ == "__main__":
    sys.exit(main())

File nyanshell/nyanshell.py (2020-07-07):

import argparse
import cmd
import glob
import io
import logging
import os
import platform
import sys
import tempfile
import subprocess
import time
import shutil

import colorama
import serial
from mp import mpfshell
from mp.mpfshell import MpFileShell
from mp.conbase import ConError
#from mp.mpfexp import MpFileExplorer, MpFileExplorerCaching, RemoteIOError
from mp.mpfexp import RemoteIOError
from mp.pyboard import PyboardError
from mp.tokenizer import Tokenizer

from nyan_explorer import NyanExplorer, NyanExplorerCaching
from telem_receiver import TelemReceiver


class NyanShell(mpfshell.MpFileShell):
    """Extension of MPFShell that adds NyanSat-specific features"""

    GYRO_CALIBRATION_MESSAGE = "To calibrate the gyroscope, let the sensor rest on a level surface for a few seconds."
    ACCEL_CALIBRATION_MESSAGE = "To calibrate the accelerometer, slowly move the sensor into >=6 distinct orientations,\nsome perpendicular to the xyz axes."
    MAGNET_CALIBRATION_MESSAGE = "To calibrate the magnetometer, move the sensor in figure-8 shapes through the air a few times."

    def __init__(self, color=False, caching=False, reset=False):
        """Creates Cmd-based shell object.

        Keyword arguments:
        color -- support colored text in the shell
        caching -- support caching the results of functions like 'ls'
        reset -- hard reset device via DTR. (serial connection only)
        """
        if color:
            colorama.init()
            cmd.Cmd.__init__(self, stdout=colorama.initialise.wrapped_stdout)
        else:
            cmd.Cmd.__init__(self)

        self.emptyline = lambda : None

        if platform.system() == "Windows":
            self.use_rawinput = False

        self.color = color
        self.caching = caching
        self.reset = reset

        self.fe = None
        self.repl = None
        self.tokenizer = Tokenizer()

        self.__intro()
        self.__set_prompt_path()

        self.emptyline = lambda : None
        self.prompts = {
                "gps_uart_tx": ("GPS UART TX pin#: ", int),
                "gps_uart_rx": ("GPS UART RX pin#: ", int),
                "i2c_servo_scl": ("Servo SCL pin#: ", int),
                "i2c_servo_sda": ("Servo SDA pin#: ", int),
                "i2c_bno_scl": ("BNO055 SCL pin#: ", int),
                "i2c_bno_sda": ("BNO055 SDA pin#: ", int),
                "i2c_screen_scl": ("Screen SCL pin#: ", int),
                "i2c_screen_sda": ("Screen SDA pin#: ", int),
                "elevation_servo_index": ("Servo default elevation index: ", float),
                "azimuth_servo_index": ("Servo default azimuth index: ", float),
                "elevation_max_rate": ("Servo elevation max rate: ", float),
                "azimuth_max_rate": ("Servo azimuth max rate: ", float)
        }
        self.antenna_initialized = False

        self.telem_receiver = None

    def __intro(self):
        """Text that appears when shell is first launched."""
        if self.color:
            self.intro = (
                "\n"
                + colorama.Fore.GREEN
                + "** Welcome to NyanSat File Shell ** "
                + colorama.Fore.RESET
                + "\n"
            )
        else:
            self.intro += (
                "\n** Welcome to NyanSat File Shell **\n"
            )

        self.intro += "-- Running on Python %d.%d using PySerial %s --\n" % (
            sys.version_info[0],
            sys.version_info[1],
            serial.VERSION,
        )
    def __is_open(self):
        """Check if a connection has been established with an ESP32."""
        if self.fe is None:
            self._MpFileShell__error("Not connected to device. Use 'open' first.")
            return False

        return True

    def __set_prompt_path(self):
        """Prompt that appears at the beginning of every line in the shell."""
        if self.fe is not None:
            pwd = self.fe.pwd()
        else:
            pwd = "/"

        if self.color:
            self.prompt = (
                colorama.Fore.BLUE
                + "nyanshell ["
                + colorama.Fore.YELLOW
                + pwd
                + colorama.Fore.BLUE
                + "]> "
                + colorama.Fore.RESET
            )
        else:
            self.prompt = "nyanshell [" + pwd + "]> "

    def __connect(self, port):
        """Attempt to connect to the ESP32.

        Arguments:
        port -- (see do_open). Specify how to connect to the device.
        """
        try:
            self._MpFileShell__disconnect()

            if self.reset:
                print("Hard resetting device ...")
            if self.caching:
                self.fe = NyanExplorerCaching(port, self.reset)
            else:
                self.fe = NyanExplorer(port, self.reset)
            print("Connected to %s" % self.fe.sysname)
            self.__set_prompt_path()
            return True
        except PyboardError as e:
            logging.error(e)
            self._MpFileShell__error(str(e))
        except ConError as e:
            logging.error(e)
            self._MpFileShell__error("Failed to open: %s" % port)
        except AttributeError as e:
            logging.error(e)
            self._MpFileShell__error("Failed to open: %s" % port)
        return False

    def antkontrol_exception(func):
        """Decorator to handle cases where the AntKontrol object on the ESP32 stops responding."""
        def exception_wrapper(*args, **kwargs):
            try:
                return func(*args, **kwargs)
            except PyboardError:
                args[0]._MpFileShell__error("The AntKontrol object is not responding. Restart it with 'antkontrol'")

        return exception_wrapper

    def _config_set(self, key, val):
        """Set an individual parameter in the config file.

        Arguments:
        key -- name of config parameter. Tab complete to see choices.
        val -- value of paramter
        """
        if isinstance(val, int) or isinstance(val, float):
            self.do_exec("config.set(\"%s\", %d)" % (key, val))
        elif isinstance(val, str):
            self.do_exec("config.set(\"%s\", %s)" % (key, val))

    def _config_get(self, key):
        """Get the value of an individual config parameter.

        Arguments:
        key -- name of config parameter.
        """
        command = "config.get(\"{}\")".format(key)
        return self.fe.eval_string_expr(command)

    def _which_config(self):
        """Get the name of the currently used config file."""
        return self.fe.eval_string_expr("config.current_file()")

    def do_open(self, args):
        """open <TARGET>
        Open connection to device with given target. TARGET might be:
        - a serial port, e.g.       ttyUSB0, ser:/dev/ttyUSB0
        - a telnet host, e.g        tn:192.168.1.1 or tn:192.168.1.1,login,passwd
        - a websocket host, e.g.    ws:192.168.1.1 or ws:192.168.1.1,passwd
        """
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

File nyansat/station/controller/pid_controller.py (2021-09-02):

import random
import time
import machine
from simple_pid.PID import PID
from controller.controller import PlatformController
from imu.imu import ImuController
from motor.motor import ServoController
from config.config import Config

class PIDPlatformController(PlatformController):
    """
    Control the antenna motion device of the antenny.
    """

    def __init__(
            self,
            azimuth: ServoController,
            elevation: ServoController,
            imu: ImuController,
            pid_output_limits: tuple = (-20, 20),
            pid_frequency: int = 100,
            p: float = 1.0,
            i: float = 0.0,
            d: float = 0.0,
    ):
        self.azimuth = azimuth
        self.elevation = elevation
        self.imu = imu
        self._motion_started = False
        self.pin_interrupt = True
        self.deadzone = None
        self.timer_id = Config('antenny').get('pid_timer_id')
        print("PID controller using timer hardware id: %d" % (self.timer_id))
        self.pid_loop_timer = machine.Timer(self.timer_id)
        self.elevation.set_position(int((self.elevation.get_max_position() - self.elevation.get_min_position()) / 2))
        self.azimuth.set_position(int((self.azimuth.get_max_position() - self.azimuth.get_min_position()) / 2))
        self.new_elevation = 0
        self.new_azimuth = 0
        self.pid_output_limits = pid_output_limits
        self.pid_frequency = pid_frequency
        self.p = p
        self.i = i
        self.d = d
        self.elevation_pid = None
        self.azimuth_pid = None
        self.init_pid()

    def init_pid(self):
        self.elevation_pid = PID(
            setpoint=self.new_elevation,
            output_limits=self.pid_output_limits,
            Kp=self.p,
            Ki=self.i,
            Kd=self.d
        )
        self.azimuth_pid = PID(
            setpoint=self.new_azimuth,
            output_limits=self.pid_output_limits,
            Kp=self.p,
            Ki=self.i,
            Kd=self.d
        )

    def start(self):
        self.start_pid_loop()

    def stop(self):
        self.stop_pid_loop()

    def set_azimuth(self, azimuth):
        """
        Sets the platform to point at a specified azimuth
        :param azimuth:
        :return:
        """
        if self.deadzone is None:
            print("You must orient the device before setting its coordinates!")
            return
        for dead_zone_min, dead_zone_max in self.deadzone:
            if dead_zone_min < azimuth < dead_zone_max:
                print("That coordinate is out of the servo limit, please realign your platform and re-orient")
                return
        self.new_azimuth = azimuth

    def get_azimuth(self):
        """
        Gets the current azimuth of the platform
        :return:
        """
        return self.imu.get_azimuth()

    def set_elevation(self, elevation):
        """
        Sets the platform to point at a specified elevation
        :param elevation:
        :return:
        """
        elevation = elevation
        self.new_elevation = elevation

    def get_elevation(self):
        """
        Gets the current elevation of the platform
        :return:
        """
        return self.imu.get_elevation()

    def start_pid_loop(self):
        """
        Initializes the PID timer interrupt
        :return:
        """
        self.new_elevation = self.imu.get_elevation()
        self.new_azimuth = self.imu.get_azimuth()
        self.azimuth_pid.setpoint = self.new_azimuth
        self.elevation_pid.setpoint = self.new_elevation
        self.pid_loop_timer.init(period=self.pid_frequency, mode=machine.Timer.PERIODIC, callback=self.__pid_loop)

    def stop_pid_loop(self):
        """
        Stops the PID timer
        :return:
        """
        self.pid_loop_timer.deinit()

    def set_coordinates(self, azimuth, elevation):
        """
        Sets relative coordinates to point at
        :param error:
        :param azimuth:
        :param elevation:
        :return:
        """
        self.set_elevation(elevation)
        self.set_azimuth(azimuth)

    def __pid_loop(self, timer):
        """
        PID ISR
        :return:
        """
        self.elevation_pid.setpoint = self.new_elevation
        self.azimuth_pid.setpoint = self.new_azimuth
        _elevation = self.get_elevation()
        _azimuth = self.get_azimuth()
        el_duty = int(self.elevation_pid(_elevation))
        az_duty = int(self.azimuth_pid(_azimuth)) * -1
        self.elevation.step(el_duty)
        self.azimuth.step(az_duty)
        # print("""
        # azimuth: {}
        # azimuth_duty: {}
        # elevation: {}
        # elevation_duty: {}
        # """.format(_azimuth, az_duty, _elevation, el_duty))

    def auto_calibrate_accelerometer(self):
        """
        Uses the servos to calibrate the accelerometer
        :return:
        """
        old_mode = self.imu.prepare_calibration()
        accel_level = self.imu.get_accelerometer_status()
        prev_accel_level = accel_level
        print("Calibrating accelerometer")
        print("Configuration level: {}".format(accel_level))
        start = time.time()
        while accel_level < 3:
            if time.time() - start > 2:
                self.elevation.set_position(
                    random.randint(
                        self.elevation.get_min_position(),
                        self.elevation.get_max_position()
                    )
                )
                self.azimuth.set_position(
                    random.randint(
                        self.azimuth.get_min_position(),
                        self.azimuth.get_max_position()
                    )
                )
                start = time.time()
            accel_level = self.imu.get_accelerometer_status()
            if accel_level != prev_accel_level:
                print("Configuration level: {}".format(accel_level))
                prev_accel_level = accel_level
        print("Accelerometer calibration done!")
        self.imu.mode(old_mode)
        return self.imu.save_accelerometer_calibration()
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

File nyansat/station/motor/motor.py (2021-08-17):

class PWMController(object):
    """Controls the PWM controller over I2C"""
    def reset(self):
        """
        Resets the device
        :return:
        """
        raise NotImplementedError()

    def freq(self, freq=None):
        """
        Sets the output pwm frequency for all channels in Hz
        :param freq:
        :return:
        """
        raise NotImplementedError()

    def pwm(self, index, on=None, off=None):
        """
        Sets the pwm output for a given pwm pin
        :param index:
        :param on:
        :param off:
        :return:
        """
        raise NotImplementedError()

    def duty(self, index, value=None, invert=False):
        """
        Sets the duty cycle for a given pwm pin
        :param index:
        :param value:
        :param invert:
        :return:
        """
        raise NotImplementedError()


class ServoController(object):
    def set_min_position(self, min_us):
        """
        Sets the minimum duty cycle that will move the servo
        :param min_us:
        :return:
        """
        raise NotImplementedError()

    def get_min_position(self):
        """
        Gets the minimum duty cycle that will move the servo
        :return:
        """
        raise NotImplementedError()

    def set_max_position(self, max_us):
        """
        Sets the maximum duty cycle that will move the servo
        :param max_us:
        :return:
        """
        raise NotImplementedError()

    def get_max_position(self):
        """
        Gets the maximum duty cycle that will move the servo
        :return:
        """
        raise NotImplementedError()

    def set_position(self, position):
        """
        Sets the position of the servo
        :param us: Use microseconds instead of duty cycle width
        :param position:
        :return:
        """
        raise NotImplementedError()

    def get_position(self):
        """
        Gets the position of the servo
        :return:
        """
        raise NotImplementedError()

    def step(self, d=1):
        """
        Steps by a given unit d
        :param d:
        :return:
        """
        raise NotImplementedError()

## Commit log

2020-06-21 dumb bugs be gone
    [antenny.py]
2020-06-23 Replace some magic numbers with config values
    [antenny.py]
2020-06-29 Minor configuration error; scl for BNO was 19, should have been 18
    [config.py]
2020-06-30 Add comments and fix initial load
    [config.py]
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2020-06-30 Refactor config to improve and fix minor bugs
    [config.py]
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2020-07-01 IMU calibration commands
    Functions in mpfshell:
    - do_calibrate
    - do_save_calibration
    - do_upload_calibration
    Added calibration register fields in config.py
    Board functions in calibration.py
2020-07-02 Add polling in IMU calibration command
    Waits for user to calibrate. Provides messages to user once calibration
    is complete for each sensor. Prods the user periodically if it takes long
    enough, telling user whicih sensors still need calibration.
    Does not yet implement the static text overriding feature.
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2020-07-02 Auto-refreshing calibration update/status panel
    The text overwrites itself so there's no big chunk of garbage
    floating down the terminal screen
2020-07-02 Moved calibration code into antenny/AntKontrol
    Should work better, use only 1 bno object. Removed calibration.py
2020-07-02 Adds mostly-finished motortest, fixes for mpfshell
    [antenny.py, servtor.py]
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2020-07-06 Initial refactor of BNO/IMU code
    - Added imu interface and separate bno055 controller
    - Remaining:
    - remove private methods from imu interface
    - extend calibration_status beyond boolean binary option
2020-07-06 Quick fix to Bno055Controller: typo in mode switch
2020-07-06 Initial refactor of servo mux/pwm driver code
    - Added motor_controller interface and PCA9685 controller
2020-07-06 Pull TelemetrySenderUDP and AntGPS out of antenny
    - Also remove typing library from imports (this is running on board)
2020-07-06 First pass refactored antenny
    - Removed: tank code, servtor.py
    - Removed functions: auto_calibration, save_ant_calib, load_ant_calib,
    calibrate_elevation, calibration_routine
    - some of these will have to be altered outside of antenny as well
    - What remains: have to factor screen code out of antenny
    lots of docstrings
2020-07-06 Changes to bno/imu: add calibration_status()
    ... for compatibility with existing shell calibration command.
    Also removed private functions from the interface class
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2020-07-07 Quick fix to get calibration functional again
    To get this functionally out of the way first; make more extensive
    changes later.
    [nyanshell.py]
2020-07-07 Fix telemetry command to use updated receiver
    [nyanshell.py]
2020-07-07 Fixed abstract base class & dataclasses incompatibility issue on micropython by refactoring the code; can import antenny now. Will take a look at functionality with the next commit
    [antenny.py, gps.py, gps_basic.py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]
2020-07-07 Fix imports to conform to others' style
    [antenny.py, gps_basic.py]
2020-07-07 Implement the UDP client. Fix the sender to use the same format as the client
    [sender_udp.py]
2020-07-07 Had import issues with sender; fixed that and updated the esp install script
    [sender_udp.py]
2020-07-07 Fix a couple of import issues/missing errors
    [__main__.py]
2020-07-07 Revised the correct way to move the motor using smooth_move
    [antenny.py]
2020-07-08 Error checking in do_antkontrol
    [__main__.py]
2020-07-08 Fixes for telemetry, telemetry client
    And some other stuff: update to match config refactor,
    UI design tweaks
    [__main__.py, antenny.py, sender_udp.py]
2020-07-08 Fixes for shell calibration routine
    [__main__.py, imu.py, imu_bno055.py]
2020-07-08 Fixed bug where esp32 would not connect to wifi until rebooted during installation procedure
2020-07-08 Fixed 'open' bug in which initiating a connection to the esp32 succeeds, but the shell drops
    [__main__.py]
2020-07-08 Fixed main.py's import statement; properly creates an AntKontrol object now
    [main.py]
2020-07-08 Fixes boot.py to start webrepl interface
    [boot.py]
2020-07-08 Fix I2C BNO pinout defaults
    [config.py]
2020-07-08 Basic try/except for disconnection when reseting through repl
    [__main__.py]
2020-07-09 Fixes error checking for configs/set/setup/switch
    [__main__.py]
2020-07-13 Add Antenny Board open source
    [01_powersupply.SchDoc, 02_USB2UART.SchDoc, 03_pushswitch.SchDoc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]
2020-07-14 Add fixes for setting up
    - Fix submodule initialization in Makefile
    - Correct procedure to run shell listed in README
    - Put screen initialization in try/except
    [antenny.py]
2020-07-16 Adds threading, cleans up, adds error checking to track mode
    [__main__.py]
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2020-07-22 Fix installer, add 'make clean', change submodules to https for easy clone, boot.py & main.py modifications
    [boot.py, main.py]
2020-07-22 Made new calibration routine based on Ang's request, no more PID (for now)
2020-07-23 Fixed calibration issues for duty cycle
    [antenny.py]
2020-07-23 Modified motor init to set option for i2c address; changed default config to reflect the configuration of Antenny V2
2020-07-23 Refactored calibration code to be axis independent; new wrapper pwm calibration function uses the refactored subroutine to calibrate both azimuth and elevation now
2020-07-23 Pinout and motor driver address changes required to get Antenny V2 board to work
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2020-07-25 switch_config command renamed switch
    switch_config has been renamed to switch. Updating documentation to match
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2020-07-27 Added i2ctest command, fixed minor errors with chained i2c bus
    [__main__.py, antenny.py]
2020-07-27 Fixed i2ctest and refactored the command code to not be in try except block longer than it needs to be
    [__main__.py]
2020-07-27 Added message to remind user to restart AntKontrol instance after running i2ctest command
2020-07-27 Added onto SAFE MODE functionality by using mock motor controller when real one is not found; PEP-8 conformance
2020-07-27 I2C devices all have configurable addresses now, all of which can be set via command; program behavior is now more properly documented so users are not caught as off guard
2020-07-27 Independent I2C Channels now use auto addresses if the configuration address does not properly configure a device. The program also logs what parameters are used, what modes it enters, and displays m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
2020-07-27 Exposed crystal parameter in the BNO wrapper class; fixed regression that prevented users from reinitializing AntKontrol
    [__main__.py, imu_bno055.py]
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2020-07-28 Fixed error with servo config; fixed TUI banner so it does not mislead users into thinking the device _itself_ is not connected; the AxisControl class now uses smooth_move
    [__main__.py, antenny.py, config.py]
2020-07-28 Fixed slight error; I had the motor and bno backwards
    [antenny.py]
2020-07-28 Motor should no longer move at start up; fixed movement parameters to go a tad faster; fixed some stability issues by doing more robust variable error checking
    [antenny.py]
2020-07-28 Fixed a typing issue where a function expects int, but should really be float; added in O'Brien's motor controller movement start and stop code
    [antenny.py]
2020-07-28 Fixed mock motor controller to have get_position function
    [antenny.py, mock_motor.py, motor_pca9685.py]
2020-07-28 Refactored command code; verbose error messages, along with infrastructure to display error messages on the board now exposed
    [__main__.py, config.py]
2020-07-29 Finished refactoring and adding verbose error messages
    [__main__.py]
2020-07-29 Fixed a few argument parsing issues for motortest, elevation, and azimuth
    [__main__.py]
2020-07-29 Some commands failed to run, but required minor rework to get back and rrunning
    [__main__.py]
2020-07-29 Added 'bnotest' and 'pwmtest' commands
    For bnotest: checks I2C bus usable; I2C addresses detected; BNO connection established; BNO calibrated
    For pwmtest: checks I2C bus usable; I2C addresses detected; PCA connection established
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2020-07-29 Fixed some regressions regarding arguments on the calibration functions; I've noted several issues with error handling that need to be addressed, mainly with the PyboardError's being raised in NyanEx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
    [__main__.py]
2020-07-30 Temporary error handling within the shell itself; should be refactored soon
    [__main__.py]
2020-07-30 Error handling for the 'antkontrol start' command. Not proper by any means and should be replaced asap.
    [__main__.py]
2020-07-30 Missing args variable in 'do_configs' function
    [__main__.py]
2020-07-30 Restructured antenna controller initialization to catch any config file errors and use default values when necessary
    [__main__.py, antenny.py]
2020-07-30 First draft of refactor (NOT WORKING YET)
    [__main__.py, antenny_client.py, cli_arg_parser.py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]
2020-07-30 Initial config infinite loop fix
    Config file architecture had the ability to enter infinite loops if
    config files pointed at one another. This initial fix tries to eliminate
    that by checking if the file to be loaded has already been loaded,
    suggesting that there is a cycle.
    This fix also prevents creating cycles by default.
    [config.py]
2020-07-30 Continue refactor. AntKontrol, el/az, upload/save, some others are done. (NOT WORKING YET)
    [__main__.py, antenny_client.py, errors.py]
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2020-07-31 Surround logging in try/except to fix ImportError
    [config.py]
2020-07-31 Replaces if-clause with guard_config_status()
    [antenny_client.py]
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2020-07-31 Begin adding command invoker, replacement for nyan_explorer. NOT WORKING YET
    [__main__.py, antenny_client.py, command_invoker.py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]
2020-07-31 Adds command_invoker, replacement for nyan_explorer
    [__main__.py, antenny_client.py, command_invoker.py]
2020-07-31 Invoker-related fixes (__main__ should not be aware of invoker)
    [__main__.py]
2020-07-31 Raising appropriate errors in invoker. Refactor track.
    [__main__.py, antenny_client.py, command_invoker.py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]
2020-07-31 Fixed typo in __main__
    [__main__.py]
2020-07-31 First pass QA. Fixes CLI crashes (adds new exception handler for do_somethings), is_open guard issue
    [__main__.py, antenny_client.py, cli_arg_parser.py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]
2020-07-31 Initial refactor of 'calibrate'
    - Split functions into MVC
    - Moved printing functions into TerminalPrinter
2020-07-31 Fixes error Josh found with running commands before 'open'
    [__main__.py, antenny_client.py, errors.py]
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2020-07-31 Adds error traceback printing (should be working)
    [errors.py]
2020-07-31 Attempt to fix PCA9685 AssertionError/IndexError
    [motor_pca9685.py]
2020-07-31 Make PCA9685 fix less naive
    [motor_pca9685.py]
2020-07-31 Fixes QA issues with setup
    [__main__.py, antenny_client.py, command_invoker.py]
2020-08-01 Attempts fix at config import error
    [command_invoker.py, errors.py]
2020-08-01 Fixed SafeMode Warning, as per Alex K's suggestion; also added in the 'startmotion' command as a test to see how simple it is to extend the new shell architecture; two thumbs up from me :
    [__main__.py, antenny_client.py, command_invoker.py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]
2020-08-01 Per Joshua's request, i2ctest doesn't run without a connection
    [antenny_client.py]
2020-08-01 Fixes track and cancel
    [__main__.py, antenny_client.py]
2020-08-03 Fixes missing help documentation for commands with decorator
    [errors.py]
2020-08-03 Fixes issue with wrong port crashing shell
    [antenny_client.py]
2020-08-03 Debug messages are more clear for calibrate and setup, per Paul's request
2020-08-03 More robust import checking; should not fail if logging doesn't work
    [main.py]
2020-08-03 Unfortunately, installing logging via the 'main.py' does not work. Regressing
    [main.py]
2020-08-04 Fix to parse lat/long as float from config
    [antenny_client.py]
2020-08-04 Draft of pin23 motor test (debouncing issue)
    [__main__.py, antenny.py]
2020-08-05 Fixed regression in 'antenny_client' for only azimuth commands
    [antenny_client.py]
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2020-08-05 Fixed interrupt functionality requested by Hans
    [antenny.py]
2020-08-05 Interrupt functionality is only available on Pin 4; this is to retain compatibility with the DIY community instructions
2020-08-05 Antenny Board Version is asked for during setup; this is an addition to aob's i2c floating check
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2020-08-05 Fixed major crash of shell when bnotest and pwmtest are called before device connection is made
    [antenny_client.py]
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2020-08-06 Hotfix for IMU issues Andres was having
    [antenny.py]
2020-08-06 Add more informative errmsg to elevation/azimuth
    - Previously, error message in red only mentioned antkontrol
    - Now raises the possibility of a 'startmotion' issue
    - Also applies to 'track' command since elev/az are used there
    [command_invoker.py, errors.py]
2020-08-07 Reintroduced pwm_calibrate function within Antenny using the new API. The functionality is not exposed to the shell yet; some API changes to the motor class will likely need to be introduced
2020-08-07 Fixed old TerminalPrinter syntax in __main__.py
    [__main__.py, antenny_client.py]
2020-08-25 finished Antenny v3 board and IMU v2
    [01_powersupply.SchDoc, 02_USB2UART.SchDoc, 03_pushswitch.SchDoc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]
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2020-08-28 Add Antenny v3 board and IMU v2 board Gerber files and NC Drill files for manufature
    [Antenna_base_v2.GBL, Antenna_base_v2.GBO, Antenna_base_v2.GBP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]
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2020-09-24 Add Kicad project for Antenny_V4
    [01_powersupply.sch, 02_USB2UART.sch, 03_pushswitch.sch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]
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2020-10-20 Finished Antenny v5 board
    [01_powersupply.SchDoc, 02_USB2UART.SchDoc, 03_pushswitch.SchDoc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]
2020-10-20 upload Gerber and NC for Antenny v5
    [Antenna_base_v5.GBL, Antenna_base_v5.GBO, Antenna_base_v5.GBP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]
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2021-08-02 small api fixes and command invoker
    [api.py, command_invoker.py, controller.py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]
2021-08-04 DefCon 29 Antenny V6
    [01_POWER_SUPPLY.SchDoc, 02_USB2UART.SchDoc, 03_PUSHBUTTON.SchDoc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]
2021-08-11 bno08x works, PID controller not working yet
    [api.py, imu_bno08x_i2c.py, imu_bno08x_rvc.py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]
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2021-09-02 fixed screen timer id, added debug message to show hardware timer id used for each controller
    [gps_location_controller.py, imu_bno08x_rvc.py, pid_controller.py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]
2021-09-02 fixed typo in default.json
    [config.py]
